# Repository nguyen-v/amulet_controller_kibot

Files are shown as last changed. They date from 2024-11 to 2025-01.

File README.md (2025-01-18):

<p align="center" width="100%">
  
</p>

<h1 align="center">Λmulet Motion Controller</h1>

<p align="center" width="100%">
  <a href="https://github.com/nguyen-v/amulet_controller_kibot/actions/workflows/ci.yaml">
    
  </a>
</p>

ΛMULET is a high-power brushless motor controller, compatible with the [moteus firmware](https://github.com/mjbots/moteus). It was specifically designed to be integrated in [EPFL Xplore](https://github.com/EPFLXplore)'s Legged Robot actuators.

<p align="center" width="100%">
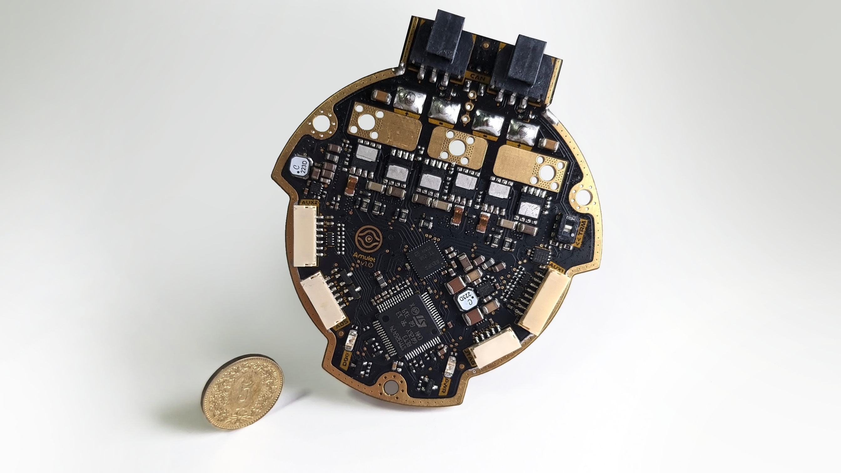
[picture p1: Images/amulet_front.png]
    
</p>

***

<p align="center">
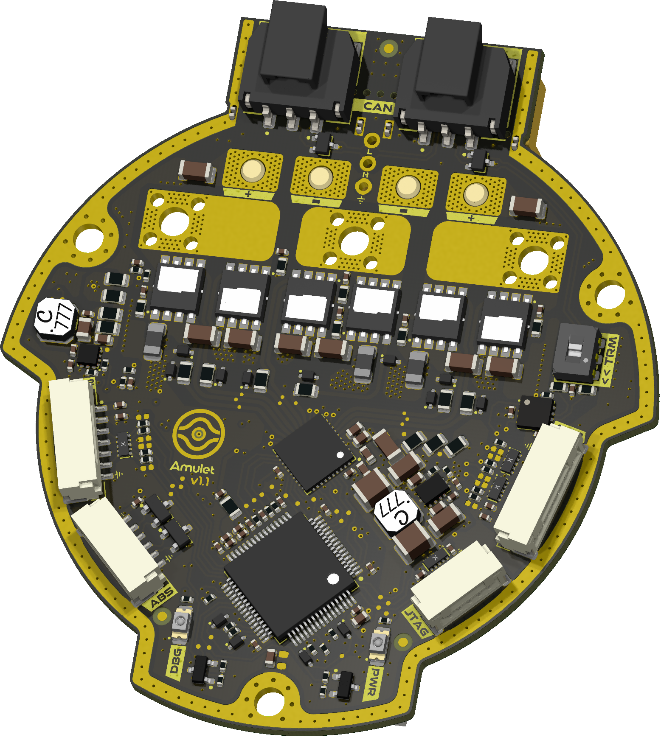
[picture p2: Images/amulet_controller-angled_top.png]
3D Top Angled
  
&nbsp; &nbsp; &nbsp; &nbsp;
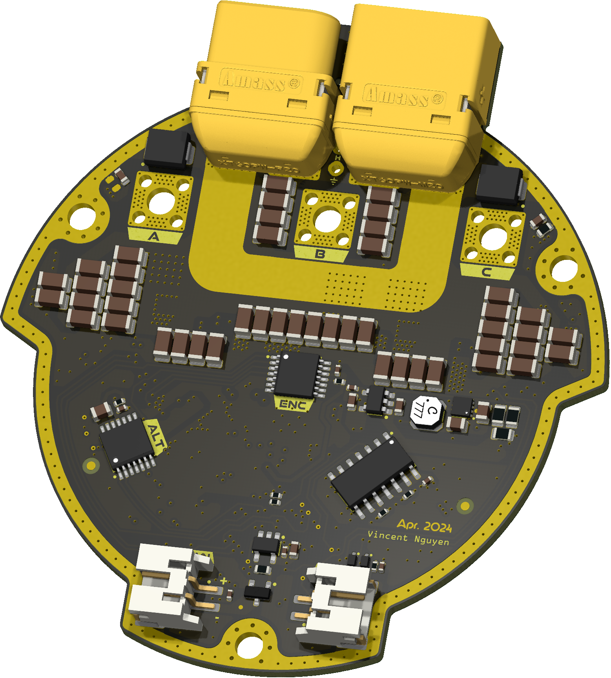
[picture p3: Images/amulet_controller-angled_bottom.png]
3D Bottom Angled
  
</p>

***

## SPECIFICATIONS

| Parameter | ΛMULET V1.0 | 
| --- | --- |
| Voltage Input | 12-44V |
| Peak Electrical Power | TBD |
| Mass | TBD |
| Peak Phase Current | 100A |
| Communication | 5Mbps CAN-FD |
| Cooling | 12V Fan |
| Positioning | 2x Onboard 14-bit Encoders |
| Control rate | 15-30kHz |
| PWM Switching Rate | 15-60kHz |
| MCU | STM32G474 |
| Dimensions | 69.67 × 76.7 mm |

***

## DIRECTORY STRUCTURE

    .
    ├─ Computations       # Misc calculations
    ├─ DXF_SVG            # Vector graphics
    ├─ HTML               # HTML files for generated webpage
    ├─ Images             # Pictures and renders
    │
    ├─ kibot_resources    # External resources for KiBot
    │  ├─ colors          # Color theme for KiCad
    │  ├─ fonts           # Fonts used in the project
    │  ├─ scripts         # External scripts used with KiBot
    │  └─ templates       # Templates for KiBot generated reports
    │
    ├─ kibot_yaml         # KiBot YAML config files
    ├─ KiRI               # KiRI (PCB diff viewer) files
    │
    ├─ lib                # KiCad footprint and symbol libraries
    │  ├─ 3d_models       # Component 3D models
    │  ├─ lib_fp          # Footprint libraries
    │  └─ lib_sym         # Symbol libraries
    │
    ├─ Logos              # Logos
    │
    ├─ Manufacturing      # Assembly and fabrication documents
    │  ├─ Assembly        # Assembly documents (BoM, pos, notes)
    │  │
    │  └─ Fabrication     # Fabrication documents (ZIP, notes)
    │     ├─ Drill Tables # CSV drill tables
    │     └─ Gerbers      # Gerbers
    │
    ├─ Report             # Reports for ERC/DRC
    ├─ Schematic          # PDF of schematic
    ├─ Templates          # Title block templates
    ├─ Testing
    │  └─ Testpoints      # Testpoints tables      
    │
    └─ Variants           # Outputs for assembly variants

***

## FIRMWARE

[Associated firmware](https://github.com/EPFLXplore/XRE_moteus/tree/amulet) is forked from the [moteus](https://github.com/mjbots/moteus) repository.

***

## CREDITS

Schematic is hugely inspired by the moteus controllers designed by Josh Pieper. They were modified to meet our own specifications, and to follow what I personally consider good layout practices.

***

## PHOTOS

<p align="center" width="100%">
    
</p>

<p align="center" width="100%">
    
</p>

<p align="center" width="100%">
    
</p>

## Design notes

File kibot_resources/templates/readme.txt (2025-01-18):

<p align="center" width="100%">
  
</p>

<h1 align="center">${BOARD_NAME}</h1>

<p align="center" width="100%">
  <a href="${GIT_URL}/actions/workflows/ci.yaml">
    CI Badge
  </a>
</p>

ΛMULET is a high-power brushless motor controller, compatible with the [moteus firmware](https://github.com/mjbots/moteus). It was specifically designed to be integrated in [EPFL Xplore](https://github.com/EPFLXplore)'s Legged Robot actuators.

<p align="center" width="100%">
    
</p>

***

<p align="center">
  3D Top Angled
&nbsp; &nbsp; &nbsp; &nbsp;
  3D Bottom Angled
</p>

***

## SPECIFICATIONS

| Parameter | ΛMULET V1.0 | 
| --- | --- |
| Voltage Input | 12-44V |
| Peak Electrical Power | TBD |
| Mass | TBD |
| Peak Phase Current | 100A |
| Communication | 5Mbps CAN-FD |
| Cooling | 12V Fan |
| Positioning | 2x Onboard 14-bit Encoders |
| Control rate | 15-30kHz |
| PWM Switching Rate | 15-60kHz |
| MCU | STM32G474 |
| Dimensions | ${bb_w_mm} × ${bb_h_mm} mm |

***

## DIRECTORY STRUCTURE

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

***

## FIRMWARE

[Associated firmware](https://github.com/EPFLXplore/XRE_moteus/tree/amulet) is forked from the [moteus](https://github.com/mjbots/moteus) repository.

***

## CREDITS

Schematic is hugely inspired by the moteus controllers designed by Josh Pieper. They were modified to meet our own specifications, and to follow what I personally consider good layout practices.

***

## PHOTOS

<p align="center" width="100%">
    
</p>

<p align="center" width="100%">
    
</p>

<p align="center" width="100%">
    
</p>

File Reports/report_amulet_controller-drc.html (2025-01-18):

Logo

| DRC report for amulet_controller
| PCB: amulet_controller Revision: 1.1.1+ (Unreleased) Date: 2025-01-18T22:40:42+0000 KiCad Version: 8.0.6 | Errors: 11 Warnings: 22 Total: 33

Violations

Type | Description | Details
clearance | Clearance violation (board minimum clearance 0.2000 mm; actual 0.0379 mm) | @(129.96 mm, 84.040001 mm): Pad 1 [/Project Architecture/Motor Control - Top Level/SC_P] of NT11 on L1 (Sig, PWR) @(129.76 mm, 83.09 mm): Pad 2 [/Project Architecture/Motor Control - Top Level/Motor Control - Inverter/SRC_LS_C] of R18 on L1 (Sig, PWR)
courtyards_overlap | Courtyards overlap | @(170.8504 mm, 87.9001 mm): Footprint U10 @(172.6404 mm, 96.4501 mm): Footprint J6
courtyards_overlap | Courtyards overlap | @(156.7504 mm, 54.1001 mm): Footprint J12 @(160.2004 mm, 61.2501 mm): Footprint D24
courtyards_overlap | Courtyards overlap | @(140.2504 mm, 54.1001 mm): Footprint J13 @(143.6504 mm, 61.2501 mm): Footprint D25
courtyards_overlap | Courtyards overlap | @(147.9 mm, 117.35 mm): Footprint C130 @(148.5004 mm, 122.0001 mm): Footprint H1
courtyards_overlap | Courtyards overlap | @(171.650401 mm, 90.100103 mm): Footprint C108 @(172.6404 mm, 96.4501 mm): Footprint J6
courtyards_overlap | Courtyards overlap | @(130.822731 mm, 107.70277 mm): Footprint J10 @(124.3404 mm, 96.4701 mm): Footprint J7
courtyards_overlap | Courtyards overlap | @(172.6404 mm, 96.4501 mm): Footprint J6 @(166.1754 mm, 107.6751 mm): Footprint J14
courtyards_overlap | Courtyards overlap | @(167.6 mm, 65.5 mm): Footprint D2 @(153.1504 mm, 64.7501 mm): Footprint J1
courtyards_overlap | Courtyards overlap | @(143.8504 mm, 64.7501 mm): Footprint J2 @(129.4 mm, 65.5 mm): Footprint D1
copper_edge_clearance | Board edge clearance violation (board setup constraints edge clearance 0.25 mm; actual 0.249999 mm) | @(132.3003 mm, 58.2043 mm): Arc on Edge.Cuts @(133.5004 mm, 58.7501 mm): PTH pad MP2 [CHASSIS] of J2
lib_footprint_mismatch | Footprint 'C_0402_1005_DensityHigh' does not match copy in library '0_capacitor_smd'. | @(165.802015 mm, 98.344758 mm): Footprint C124
lib_footprint_mismatch | Footprint '1054301203' does not match copy in library '0_connectors'. | @(156.7504 mm, 54.1001 mm): Footprint J12
lib_footprint_mismatch | Footprint 'R_0603_1608_DensityHigh' does not match copy in library '0_resistor_smd'. | @(149.1 mm, 117.35 mm): Footprint R52
lib_footprint_mismatch | Footprint 'C_0402_1005_DensityHigh' does not match copy in library '0_capacitor_smd'. | @(166.620577 mm, 95.251212 mm): Footprint C120
lib_footprint_mismatch | Footprint '1054301203' does not match copy in library '0_connectors'. | @(140.2504 mm, 54.1001 mm): Footprint J13
lib_footprint_mismatch | Footprint 'C_0402_1005_DensityHigh' does not match copy in library '0_capacitor_smd'. | @(167.243984 mm, 92.943938 mm): Footprint C118
lib_footprint_mismatch | Footprint 'C_0402_1005_DensityHigh' does not match copy in library '0_capacitor_smd'. | @(129.866333 mm, 92.694503 mm): Footprint C123
lib_footprint_mismatch | Footprint 'C_0402_1005_DensityHigh' does not match copy in library '0_capacitor_smd'. | @(167.451041 mm, 92.1712 mm): Footprint C116
lib_footprint_mismatch | Footprint 'C_0402_1005_DensityHigh' does not match copy in library '0_capacitor_smd'. | @(130.493965 mm, 95.036872 mm): Footprint C121
lib_footprint_mismatch | Footprint 'C_0402_1005_DensityHigh' does not match copy in library '0_capacitor_smd'. | @(130.701025 mm, 95.809613 mm): Footprint C119
lib_footprint_mismatch | Footprint 'C_0402_1005_DensityHigh' does not match copy in library '0_capacitor_smd'. | @(166.413521 mm, 96.023949 mm): Footprint C122
lib_footprint_mismatch | Footprint 'SOT1176D' does not match copy in library '0_package_DFN_QFN'. | @(128.472459 mm, 95.992643 mm): Footprint D17
lib_footprint_mismatch | Footprint 'C_0402_1005_DensityHigh' does not match copy in library '0_capacitor_smd'. | @(131.320291 mm, 98.127833 mm): Footprint C117
lib_footprint_mismatch | Footprint 'R_0603_1608_DensityHigh' does not match copy in library '0_resistor_smd'. | @(173.33 mm, 69.8 mm): Footprint R54
lib_footprint_mismatch | Footprint 'SOP-14_4.4x5mm_P0.65mm_H1.2mm' does not match copy in library '0_package_SO'. | @(166.253518 mm, 100.25 mm): Footprint U8
lib_footprint_mismatch | Footprint 'DIOM4336X24N' does not match copy in library '0_diode_smd'. | @(129.4 mm, 65.5 mm): Footprint D1
solder_mask_bridge | Front solder mask aperture bridges items with different nets | @(129.96 mm, 84.040001 mm): Pad 1 [/Project Architecture/Motor Control - Top Level/SC_P] of NT11 on L1 (Sig, PWR) @(129.76 mm, 83.09 mm): Pad 2 [/Project Architecture/Motor Control - Top Level/Motor Control - Inverter/SRC_LS_C] of R18 on L1 (Sig, PWR)
solder_mask_bridge | Front solder mask aperture bridges items with different nets | @(129.96 mm, 84.840001 mm): Pad 1 [/Project Architecture/Motor Control - Top Level/SC_N] of NT12 on L1 (Sig, PWR) @(129.76 mm, 85.79 mm): Pad 1 [GND] of R18 on L1 (Sig, PWR)
solder_mask_bridge | Front solder mask aperture bridges items with different nets | @(136.130445 mm, 93.156811 mm): Polygon on F.Mask @(136.0504 mm, 93.9001 mm): Via [/Project Architecture/Power - Generation/VOS_3V3] on L1 (Sig, PWR) - L6 (Sig, PWR)
solder_mask_bridge | Front solder mask aperture bridges items with different nets | @(157.7504 mm, 84.865 mm): Pad 1 [/Project Architecture/Motor Control - Top Level/SA_N] of NT6 on L1 (Sig, PWR) @(157.5754 mm, 85.79 mm): Pad 1 [GND] of R12 on L1 (Sig, PWR)
solder_mask_bridge | Front solder mask aperture bridges items with different nets | @(151.8996 mm, 84.0399 mm): Pad 1 [/Project Architecture/Motor Control - Top Level/SB_P] of NT8 on L1 (Sig, PWR) @(152.1 mm, 83.09 mm): Pad 2 [/Project Architecture/Motor Control - Top Level/Motor Control - Inverter/SRC_LS_B] of R15 on L1 (Sig, PWR)
solder_mask_bridge | Front solder mask aperture bridges items with different nets | @(151.8996 mm, 84.8399 mm): Pad 1 [/Project Architecture/Motor Control - Top Level/SB_N] of NT9 on L1 (Sig, PWR) @(152.1 mm, 85.79 mm): Pad 1 [GND] of R15 on L1 (Sig, PWR)

Generated by KiBot (https://github.com/INTI-CMNB/KiBot/) v1.8.3

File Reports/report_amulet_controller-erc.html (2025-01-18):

Logo

| ERC report for amulet_controller
| Schematic: amulet_controller Revision: 1.1.1+ (Unreleased) Date: 2025-01-18T22:40:34+0000 KiCad Version: 8.0.6 | Errors: 0 Warnings: 86 Total: 86

Sheet /Project Architecture/ (Project Architecture.kicad_sch)

Type | Description | Details
lib_symbol_issues | Symbol '+3V3' has been modified in library 'power' | @(1.9431 mm, 0.4953 mm): Symbol #PWR05 [+3V3]
lib_symbol_issues | Symbol '+5V' has been modified in library 'power' | @(1.905 mm, 0.4318 mm): Symbol #PWR04 [+5V]
lib_symbol_issues | Symbol '+12V' has been modified in library 'power' | @(1.8669 mm, 0.4953 mm): Symbol #PWR03 [+12V]

Sheet /Project Architecture/MCU - Power/ (MCU - Power.kicad_sch)

Type | Description | Details
lib_symbol_issues | Symbol 'GND' has been modified in library 'power' | @(1.4351 mm, 0.6223 mm): Symbol #PWR014 [GND]
lib_symbol_issues | Symbol '+3V3' has been modified in library 'power' | @(1.4351 mm, 0.4953 mm): Symbol #PWR013 [+3V3]
lib_symbol_issues | Symbol 'PWR_FLAG' has been modified in library 'power' | @(1.5367 mm, 0.9398 mm): Symbol #FLG01 [PWR_FLAG]
lib_symbol_issues | Symbol 'GND' has been modified in library 'power' | @(1.2827 mm, 1.0668 mm): Symbol #PWR011 [GND]
lib_symbol_issues | Symbol 'GND' has been modified in library 'power' | @(1.0414 mm, 1.1684 mm): Symbol #PWR010 [GND]
lib_symbol_issues | Symbol 'GND' has been modified in library 'power' | @(0.8128 mm, 0.8382 mm): Symbol #PWR08 [GND]
lib_symbol_issues | Symbol '+3V3' has been modified in library 'power' | @(0.8128 mm, 0.7112 mm): Symbol #PWR07 [+3V3]
lib_symbol_issues | Symbol 'GND' has been modified in library 'power' | @(1.8542 mm, 1.3081 mm): Symbol #PWR015 [GND]
lib_symbol_issues | Symbol 'GND' has been modified in library 'power' | @(1.2827 mm, 1.2573 mm): Symbol #PWR012 [GND]

Sheet /Project Architecture/MCU - IOs/ (MCU - IOs.kicad_sch)

Type | Description | Details
lib_symbol_issues | Symbol 'GND' has been modified in library 'power' | @(1.7018 mm, 1.778 mm): Symbol #PWR016 [GND]

Sheet /Project Architecture/Power - Generation/ (Power - Generation.kicad_sch)

Type | Description | Details
lib_symbol_issues | Symbol 'GND' has been modified in library 'power' | @(2.3114 mm, 2.0574 mm): Symbol #PWR020 [GND]
lib_symbol_issues | Symbol 'PWR_FLAG' has been modified in library 'power' | @(2.4257 mm, 1.143 mm): Symbol #FLG07 [PWR_FLAG]
lib_symbol_issues | Symbol 'GND' has been modified in library 'power' | @(2.3114 mm, 2.2225 mm): Symbol #PWR021 [GND]
lib_symbol_issues | Symbol 'GND' has been modified in library 'power' | @(2.3114 mm, 1.8923 mm): Symbol #PWR019 [GND]
lib_symbol_issues | Symbol 'PWR_FLAG' has been modified in library 'power' | @(1.5875 mm, 1.143 mm): Symbol #FLG04 [PWR_FLAG]
lib_symbol_issues | Symbol 'GND' has been modified in library 'power' | @(0.6477 mm, 1.524 mm): Symbol #PWR018 [GND]
lib_symbol_issues | Symbol 'PWR_FLAG' has been modified in library 'power' | @(3.175 mm, 0.5207 mm): Symbol #FLG08 [PWR_FLAG]
lib_symbol_issues | Symbol 'GND' has been modified in library 'power' | @(3.1115 mm, 1.5113 mm): Symbol #PWR023 [GND]
lib_symbol_issues | Symbol 'GND' has been modified in library 'power' | @(2.7305 mm, 0.889 mm): Symbol #PWR022 [GND]
lib_symbol_issues | Symbol 'PWR_FLAG' has been modified in library 'power' | @(0.4826 mm, 0.5207 mm): Symbol #FLG02 [PWR_FLAG]
lib_symbol_issues | Symbol 'GND' has been modified in library 'power' | @(0.6477 mm, 0.889 mm): Symbol #PWR017 [GND]
lib_symbol_issues | Symbol 'PWR_FLAG' has been modified in library 'power' | @(2.4257 mm, 0.5207 mm): Symbol #FLG06 [PWR_FLAG]
lib_symbol_issues | Symbol 'PWR_FLAG' has been modified in library 'power' | @(1.9939 mm, 0.8509 mm): Symbol #FLG05 [PWR_FLAG]
lib_symbol_issues | Symbol 'PWR_FLAG' has been modified in library 'power' | @(1.524 mm, 0.5207 mm): Symbol #FLG03 [PWR_FLAG]

Sheet /Project Architecture/Power - Connectors/ (Power - Connectors.kicad_sch)

Type | Description | Details
lib_symbol_issues | Symbol 'GND' has been modified in library 'power' | @(1.3589 mm, 0.9271 mm): Symbol #PWR024 [GND]

Sheet /Project Architecture/Motor Control - Top Level/ (Motor Control - Top Level.kicad_sch)

Type | Description | Details
lib_symbol_issues | Symbol 'GND' has been modified in library 'power' | @(1.4605 mm, 1.9685 mm): Symbol #PWR033 [GND]
lib_symbol_issues | Symbol 'GND' has been modified in library 'power' | @(1.7399 mm, 0.9652 mm): Symbol #PWR034 [GND]
lib_symbol_issues | Symbol 'GND' has been modified in library 'power' | @(1.2573 mm, 1.0922 mm): Symbol #PWR032 [GND]
lib_symbol_issues | Symbol '+3V3' has been modified in library 'power' | @(0.8255 mm, 1.7907 mm): Symbol #PWR026 [+3V3]
lib_symbol_issues | Symbol 'GND' has been modified in library 'power' | @(1.0541 mm, 0.762 mm): Symbol #PWR029 [GND]
lib_symbol_issues | Symbol '+3V3' has been modified in library 'power' | @(1.0287 mm, 1.016 mm): Symbol #PWR028 [+3V3]
lib_symbol_issues | Symbol 'GND' has been modified in library 'power' | @(1.1049 mm, 1.5875 mm): Symbol #PWR031 [GND]

Sheet /Project Architecture/Motor Control - Top Level/Motor Control - Inverter/ (Motor Control - Inverter.kicad_sch)

Type | Description | Details
lib_symbol_issues | Symbol 'GND' has been modified in library 'power' | @(0.3556 mm, 1.4224 mm): Symbol #PWR036 [GND]

Sheet /Project Architecture/Misc - Board Version, DAC/ (Misc - Board Version DAC.kicad_sch)

Type | Description | Details
lib_symbol_issues | Symbol 'GND' has been modified in library 'power' | @(1.4986 mm, 0.8128 mm): Symbol #PWR038 [GND]

Sheet /Project Architecture/User - LED Indicators/ (User - LED Indicators.kicad_sch)

Type | Description | Details
lib_symbol_issues | Symbol 'GND' has been modified in library 'power' | @(1.7653 mm, 1.1176 mm): Symbol #PWR040 [GND]
lib_symbol_issues | Symbol 'GND' has been modified in library 'power' | @(1.2827 mm, 1.1176 mm): Symbol #PWR039 [GND]
lib_symbol_issues | Symbol '+5V' has been modified in library 'power' | @(1.9812 mm, 0.5588 mm): Symbol #PWR041 [+5V]

Sheet /Project Architecture/Sensing - Temperature/ (Sensing - Temperature.kicad_sch)

Type | Description | Details
lib_symbol_issues | Symbol 'GND' has been modified in library 'power' | @(1.7653 mm, 1.1176 mm): Symbol #PWR044 [GND]
lib_symbol_issues | Symbol 'GND' has been modified in library 'power' | @(0.9779 mm, 1.1176 mm): Symbol #PWR042 [GND]

Sheet /Project Architecture/Sensing - Battery/ (Sensing - Battery.kicad_sch)

Type | Description | Details
lib_symbol_issues | Symbol 'GND' has been modified in library 'power' | @(1.3462 mm, 0.9271 mm): Symbol #PWR046 [GND]

Sheet /Project Architecture/Sensing - Position/ (Sensing - Position.kicad_sch)

Type | Description | Details
lib_symbol_issues | Symbol '+3V3' has been modified in library 'power' | @(0.508 mm, 0.6604 mm): Symbol #PWR047 [+3V3]
lib_symbol_issues | Symbol 'PWR_FLAG' has been modified in library 'power' | @(0.8001 mm, 0.6858 mm): Symbol #FLG09 [PWR_FLAG]
lib_symbol_issues | Symbol 'GND' has been modified in library 'power' | @(0.508 mm, 1.1049 mm): Symbol #PWR048 [GND]
lib_symbol_issues | Symbol 'GND' has been modified in library 'power' | @(2.2098 mm, 0.8001 mm): Symbol #PWR051 [GND]
lib_symbol_issues | Symbol 'PWR_FLAG' has been modified in library 'power' | @(2.2098 mm, 0.6858 mm): Symbol #FLG010 [PWR_FLAG]
lib_symbol_issues | Symbol '+3V3' has been modified in library 'power' | @(1.7526 mm, 0.6604 mm): Symbol #PWR049 [+3V3]
lib_symbol_issues | Symbol 'GND' has been modified in library 'power' | @(1.7526 mm, 1.1176 mm): Symbol #PWR050 [GND]

Sheet /Project Architecture/Interface - RS-422/ (Interface - RS-422.kicad_sch)

Type | Description | Details
lib_symbol_issues | Symbol '+3V3' has been modified in library 'power' | @(1.4732 mm, 0.5334 mm): Symbol #PWR054 [+3V3]
lib_symbol_issues | Symbol 'GND' has been modified in library 'power' | @(1.4605 mm, 1.0922 mm): Symbol #PWR053 [GND]
lib_symbol_issues | Symbol 'GND' has been modified in library 'power' | @(1.2827 mm, 0.6477 mm): Symbol #PWR052 [GND]

Sheet /Project Architecture/Interface - FD-CAN/ (Interface - FD-CAN.kicad_sch)

Type | Description | Details
lib_symbol_issues | Symbol '+5V' has been modified in library 'power' | @(1.7018 mm, 0.6477 mm): Symbol #PWR058 [+5V]
lib_symbol_issues | Symbol '+3V3' has been modified in library 'power' | @(1.3462 mm, 0.6477 mm): Symbol #PWR056 [+3V3]
lib_symbol_issues | Symbol 'GND' has been modified in library 'power' | @(1.7018 mm, 0.7747 mm): Symbol #PWR059 [GND]
lib_symbol_issues | Symbol 'GND' has been modified in library 'power' | @(1.2954 mm, 1.1303 mm): Symbol #PWR055 [GND]
lib_symbol_issues | Symbol 'GND' has been modified in library 'power' | @(1.3462 mm, 0.7747 mm): Symbol #PWR057 [GND]

Sheet /Project Architecture/Interface - Fan Control/ (Interface - Fan Control.kicad_sch)

Type | Description | Details
lib_symbol_issues | Symbol 'GND' has been modified in library 'power' | @(1.3589 mm, 1.0795 mm): Symbol #PWR062 [GND]
lib_symbol_issues | Symbol 'GND' has been modified in library 'power' | @(1.0414 mm, 0.7874 mm): Symbol #PWR060 [GND]
lib_symbol_issues | Symbol '+5V' has been modified in library 'power' | @(1.3589 mm, 0.6477 mm): Symbol #PWR061 [+5V]

Sheet /Project Architecture/Interface - Interconnects/ (Interface - Interconnects.kicad_sch)

Type | Description | Details
lib_symbol_issues | Symbol '+12V' has been modified in library 'power' | @(1.7653 mm, 2.5146 mm): Symbol #PWR077 [+12V]
lib_symbol_issues | Symbol 'GND' has been modified in library 'power' | @(2.6797 mm, 2.2733 mm): Symbol #PWR081 [GND]
lib_symbol_issues | Symbol 'GND' has been modified in library 'power' | @(2.6924 mm, 0.7493 mm): Symbol #PWR082 [GND]
lib_symbol_issues | Symbol 'GND' has been modified in library 'power' | @(2.7051 mm, 0.9906 mm): Symbol #PWR083 [GND]
lib_symbol_issues | Symbol 'GND' has been modified in library 'power' | @(3.5941 mm, 0.8636 mm): Symbol #PWR089 [GND]
lib_symbol_issues | Symbol '+3V3' has been modified in library 'power' | @(2.8194 mm, 1.3716 mm): Symbol #PWR086 [+3V3]
lib_symbol_issues | Symbol 'GND' has been modified in library 'power' | @(2.8575 mm, 1.4224 mm): Symbol #PWR088 [GND]
lib_symbol_issues | Symbol '+5V' has been modified in library 'power' | @(2.6797 mm, 1.8923 mm): Symbol #PWR080 [+5V]
lib_symbol_issues | Symbol 'GND' has been modified in library 'power' | @(2.7178 mm, 1.9558 mm): Symbol #PWR085 [GND]
lib_symbol_issues | Symbol 'GND' has been modified in library 'power' | @(2.8194 mm, 1.6764 mm): Symbol #PWR087 [GND]
lib_symbol_issues | Symbol 'GND' has been modified in library 'power' | @(1.8288 mm, 2.6035 mm): Symbol #PWR078 [GND]
lib_symbol_issues | Symbol 'GND' has been modified in library 'power' | @(0.6604 mm, 1.0922 mm): Symbol #PWR070 [GND]
lib_symbol_issues | Symbol 'GND' has been modified in library 'power' | @(0.6604 mm, 2.0447 mm): Symbol #PWR071 [GND]
lib_symbol_issues | Symbol '+5V' has been modified in library 'power' | @(0.5715 mm, 0.5334 mm): Symbol #PWR066 [+5V]
lib_symbol_issues | Symbol 'GND' has been modified in library 'power' | @(0.8255 mm, 0.6223 mm): Symbol #PWR074 [GND]
lib_symbol_issues | Symbol '+3V3' has been modified in library 'power' | @(0.7747 mm, 0.5334 mm): Symbol #PWR072 [+3V3]
lib_symbol_issues | Symbol 'GND' has been modified in library 'power' | @(0.6223 mm, 0.6223 mm): Symbol #PWR068 [GND]
lib_symbol_issues | Symbol '+5V' has been modified in library 'power' | @(0.5715 mm, 1.5113 mm): Symbol #PWR067 [+5V]
lib_symbol_issues | Symbol '+3V3' has been modified in library 'power' | @(0.7747 mm, 1.5113 mm): Symbol #PWR073 [+3V3]
lib_symbol_issues | Symbol 'GND' has been modified in library 'power' | @(0.6223 mm, 1.6002 mm): Symbol #PWR069 [GND]
lib_symbol_issues | Symbol 'GND' has been modified in library 'power' | @(0.8255 mm, 1.6002 mm): Symbol #PWR075 [GND]

Sheet /Project Architecture/Misc - Holes, Fiducials/ (Misc - Holes Fiducials.kicad_sch)

Type | Description | Details
lib_symbol_issues | Symbol 'PWR_FLAG' has been modified in library 'power' | @(1.1049 mm, 0.8636 mm): Symbol #FLG011 [PWR_FLAG]
lib_symbol_issues | Symbol 'GND' has been modified in library 'power' | @(1.7907 mm, 1.016 mm): Symbol #PWR095 [GND]
lib_symbol_issues | Symbol 'GND' has been modified in library 'power' | @(1.3843 mm, 1.016 mm): Symbol #PWR093 [GND]
lib_symbol_issues | Symbol 'GND' has been modified in library 'power' | @(0.9906 mm, 1.016 mm): Symbol #PWR091 [GND]

Generated by KiBot (https://github.com/INTI-CMNB/KiBot/) v1.8.3

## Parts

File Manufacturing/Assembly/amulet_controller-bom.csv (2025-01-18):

Row | Quantity Per PCB | References | Value | Datasheet | Footprint | Description | Manufacturer | Manufacturer Part Number | Supplier 1 | Supplier Part Number 1
1 | 3 | C12 C13 C14 | 1n X7R 25V | https://www.yageo.com/upload/media/product/app/datasheet/mlcc/upy-ac_np0x7rx7s_6_3v-to-2kv.pdf | C_0402_1005_DensityHigh | 1000 pF ±10% 25V Ceramic Capacitor X7R 0402 (1005 Metric) | YAGEO | AC0402KRX7R8BB102 | Digikey | 311-3065-1-ND
2 | 6 | C133 C134 C135 C136 C137 C138 | 3n3 X7R 100V | https://search.murata.co.jp/Ceramy/image/img/A01X/G101/ENG/GRM155R72A332KA01-01.pdf | C_0402_1005_DensityHigh | 3300 pF ±10% 100V Ceramic Capacitor X7R 0402 (1005 Metric) | Murata Electronics | GRM155R72A332KA01D | Digikey | 490-8261-1-ND
3 | 1 | C129 | 4n7 X7R 100V | https://www.murata.com/-/media/webrenewal/support/library/catalog/products/k35e.ashx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 | C_0402_1005_DensityHigh | 4700 pF ±10% 100V Ceramic Capacitor X7R 0402 (1005 Metric) | Murata Electronics | GCM155R72A472KA37D | Digikey | 490-4765-1-ND
4 | 1 | C76 | 10n X7R 100V | https://mm.digikey.com/Volume0/opasdata/d220001/medias/docus/2615/HMR105B7103KV-F_SS.pdf | C_0402_1005_DensityHigh | 10000 pF ±10% 100V Ceramic Capacitor X7R 0402 (1005 Metric) | Taiyo Yuden | HMR105B7103KV-F | Digikey | 587-HMR105B7103KV-FCT-ND
5 | 1 | C91 | 47n X7R 100V | https://connect.kemet.com:7667/gateway/IntelliData-ComponentDocumentation/1.0/download/datasheet/C0603C473K1RECAUTO | C_0603_1608_DensityHigh | 0.047 µF ±10% 100V Ceramic Capacitor X7R 0603 (1608 Metric) | KEMET | C0603C473K1RECAUTO | Digikey | 399-14764-1-ND
6 | 26 | C3 C4 C5 C8 C10 C11 C27 C28 C29 C101 C102 C103 C104 C105 C107 C108 C109 C111 C112 C113 C114 C115 C125 C126 C127 C128 | 100n X7R 50V | https://search.murata.co.jp/Ceramy/image/img/A01X/G101/ENG/GCM155R71H104KE02-01.pdf | C_0402_1005_DensityHigh | 0.1 µF ±10% 50V Ceramic Capacitor X7R 0402 (1005 Metric) | Murata Electronics | GCM155R71H104KE02J | Digikey | 490-14514-1-ND
7 | 2 | C22 C92 | 100n X7R 100V | https://mm.digikey.com/Volume0/opasdata/d220001/medias/docus/21/HMK107B7104KAHT_SS.pdf | C_0603_1608_DensityHigh | 0.1 µF ±10% 100V Ceramic Capacitor X7R 0603 (1608 Metric) | Taiyo Yuden | HMK107B7104KAHT | Digikey | 587-6009-1-ND
8 | 1 | C90 | 100n X7R 16V | https://search.murata.co.jp/Ceramy/image/img/A01X/G101/ENG/GCM155R71C104KA55-01.pdf | C_0402_1005_DensityHigh | 0.1 µF ±10% 16V Ceramic Capacitor X7R 0402 (1005 Metric) | Murata Electronics | GCM155R71C104KA55D | Digikey | 490-4759-1-ND
9 | 3 | C95 C97 C99 | 100n X7R 100V | https://connect.kemet.com:7667/gateway/IntelliData-ComponentDocumentation/1.0/download/datasheet/C1206C104K1RACAUTO | C_1206_3216_DensityHighest | 0.1 µF ±10% 100V Ceramic Capacitor X7R 1206 (3216 Metric) | KEMET | C1206C104K1RACAUTO | Digikey | 399-7008-1-ND
10 | 2 | C23 C25 | 220n X7S 100V | https://mm.digikey.com/Volume0/opasdata/d220001/medias/docus/2249/TMK105B7224KV-FR_SS.pdf | C_0603_1608_DensityHigh | 0.22 µF ±10% 100V Ceramic Capacitor X7S 0603 (1608 Metric) | Taiyo Yuden | HMK107C7224KAHTE | Digikey | 587-5012-1-ND
11 | 5 | C2 C6 C9 C24 C26 | 1u X7R 10V | https://search.murata.co.jp/Ceramy/image/img/A01X/G101/ENG/GRM155Z71A105KE01-01A.pdf | C_0402_1005_DensityHigh | 1 µF ±10% 10V Ceramic Capacitor X7R 0402 (1005 Metric) | Murata Electronics | GRM155Z71A105KE01J | Digikey | 490-GRM155Z71A105KE01JCT-ND
12 | 3 | C60 C88 C93 | 1u X7R 25V | https://mm.digikey.com/Volume0/opasdata/d220001/medias/docus/2146/TMK107AB7105KAHT_SS.pdf | C_0603_1608_DensityHigh | 1 µF ±10% 25V Ceramic Capacitor X7R 0603 (1608 Metric) | Taiyo Yuden | TMK107AB7105KAHT | Digikey | 587-3467-1-ND
13 | 1 | C94 | 1u X7R 6.3V | https://search.murata.co.jp/Ceramy/image/img/A01X/G101/ENG/GRT155R70J105KE01-01.pdf | C_0402_1005_DensityHigh | 1 µF ±10% 6.3V Ceramic Capacitor X7R 0402 (1005 Metric) | Murata Electronics | GRT155R70J105KE01D | Digikey | 490-18216-1-ND
14 | 7 | C15 C16 C17 C18 C20 C45 C52 | 2u2 X7R 100V | https://product.tdk.com/system/files/dam/doc/product/capacitor/ceramic/mlcc/catalog/mlcc_automotive_midvoltage_en.pdf | R_0805_2012_DensityHigh | Multilayer Ceramic Capacitors MLCC - SMD/SMT 0805 100VDC 2.2uF 10% 1.25mm AEC-Q200 | TDK Corporation | CGA4J1X7R2A225K125AC | Mouser | 810-CGA4J7R2A225K125
15 | 3 | C1 C84 C110 | 4u7 X7R 16V | https://search.murata.co.jp/Ceramy/image/img/A01X/G101/ENG/GRM188Z71C475KE21-01A.pdf | C_0603_1608_DensityHigh | 4.7 µF ±10% 16V Ceramic Capacitor X7R 0603 (1608 Metric) | Murata Electronics | GRM188Z71C475KE21J | Digikey | 490-GRM188Z71C475KE21JCT-ND
16 | 54 | C19 C21 C31 C32 C33 C34 C35 C36 C39 C40 C41 C42 C43 C44 C46 C47 C48 C49 C50 C51 C53 C54 C55 C57 C58 C59 C61 C62 C63 C64 C65 C66 C67 C68 C69 C70 C71 C72 C73 C74 C75 C77 C78 C79 C80 C81 C82 C85 C86 C87 C89 C96 C98 C100 | 4u7 X7R 100V | https://search.murata.co.jp/Ceramy/image/img/A01X/G101/ENG/GRJ31CZ72A475KE01-01.pdf | C_1206_3216_DensityHigh | 4.7 µF ±10% 100V Ceramic Capacitor X7R 1206 (3216 Metric) | Murata Electronics | GRJ31CZ72A475KE01L | Digikey | 490-GRJ31CZ72A475KE01LCT-ND
17 | 1 | C7 | 4u7 X5R 25V | https://www.mouser.ch/datasheet/2/40/CM_Series_e-2835982.pdf | C_0402_1005_DensityHigh | 4.7 µF ±20% 25V Ceramic Capacitor X5R 0402 (1005 Metric) | KYOCERA AVX | CM05X5R475M25AH | Mouser | 581-CM05X5R475M25AH
18 | 2 | C56 C106 | 10u X7R 25V | https://search.murata.co.jp/Ceramy/image/img/A01X/G101/ENG/GRM21BZ71E106KE15-01.pdf | C_0805_2012_DensityHighest | 10 µF ±10% 25V Ceramic Capacitor X7R 0805 (2012 Metric) | Murata Electronics | GRM21BZ71E106KE15L | Digikey | 490-GRM21BZ71E106KE15LCT-ND
19 | 2 | C30 C38 | 15u X7R 25V | https://product.tdk.com/system/files/dam/doc/product/capacitor/ceramic/mlcc/catalog/mlcc_automotive_general_en.pdf | C_1210_3225_DensityHigh | 15 µF ±20% 25V Ceramic Capacitor X7R 1210 (3225 Metric) | TDK Corporation | CGA6M3X7R1E156M200AB | Digikey | 445-175431-1-ND
20 | 2 | C37 C83 | 22u X7R 10V | https://search.murata.co.jp/Ceramy/image/img/A01X/G101/ENG/GRM21BZ71A226ME15-01.pdf | C_0805_2012_DensityHighest | 22 µF ±20% 10V Ceramic Capacitor X7R 0805 (2012 Metric) | Murata Electronics | GRM21BZ71A226ME15L | Digikey | 490-GRM21BZ71A226ME15LCT-ND
21 | 3 | C130 C131 C132 | 1n X7R 1kV | https://connect.kemet.com:7667/gateway/IntelliData-ComponentDocumentation/1.0/download/specsheet/C0603V102KDRAC7867 | C_0603_1608_DensityHigh | 1000 pF ±10% 1000V (1kV) Ceramic Capacitor X7R 0603 (1608 Metric) | KEMET | C0603V102KDRAC7867 | Digikey | 399-12306-1-ND
22 | 15 | D3 D4 D5 D6 D7 D8 D9 D10 D11 D14 D15 D19 D20 D21 D22 | BAT41KFILM | https://www.st.com/content/ccc/resource/technical/document/datasheet/5b/cd/d8/0a/45/56/41/6c/CD00130227.pdf/files/CD00130227.pdf/jcr:content/translations/en.C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 | D_SOD-523 | Diode 100 V 200mA Surface Mount SOD-523 | STMicroelectronics | BAT41KFILM | Digikey | 497-5556-1-ND
23 | 2 | D23 D27 | CDSOT23-SM712 | https://www.bourns.com/docs/Product-Datasheets/CDSOT23-SM712.pdf | SOT95P230X110-3N | 26V, 14V Clamp 17A (8/20µs) Ipp Tvs Diode Surface Mount SOT-23-3 | Bourns Inc. | CDSOT23-SM712 | Digikey | CDSOT23-SM712CT-ND
24 | 1 | D13 | GREEN | https://www.bivar.com/parts_content/Datasheets/SM1206NPGC-IL.pdf | LED_SM1206 | Green 525nm LED Indication - Discrete 3V 1206 (3216 Metric) | Bivar Inc. | SM1206NPGC-IL | Digikey | 492-1945-1-ND
25 | 2 | D24 D25 | PESD2CANFD24V-UX | https://assets.nexperia.com/documents/data-sheet/PESD2CANFD24V-U.pdf | SOT95P230X117-3N | 42V Clamp 2.6A (8/20µs) Ipp Tvs Diode Surface Mount SOT-323 | Nexperia USA Inc. | PESD2CANFD24V-UX | Digikey | 1727-PESD2CANFD24V-UXCT-ND
26 | 2 | D18 D26 | PESD4USB3U-TBSX | https://assets.nexperia.com/documents/data-sheet/PESD4USB3U-TBS.pdf | SOT1176D | 3.5V (Typ) Clamp 7A (8/20µs) Ipp Tvs Diode Surface Mount, Wettable Flank DFN2510D-10 | Nexperia USA Inc. | PESD4USB3U-TBSX | Digikey | 1727-PESD4USB3U-TBSXCT-ND
27 | 2 | D16 D17 | PESD4USB5B-TBSX | https://assets.nexperia.com/documents/data-sheet/PESD4USB5B-TBS.pdf | SOT1176D | 5.5V (Typ) Clamp 7A (8/20µs) Ipp Tvs Diode Surface Mount, Wettable Flank DFN2510D-10 | Nexperia USA Inc. | PESD4USB5B-TBSX | Digikey | 1727-PESD4USB5B-TBSXCT-ND
28 | 2 | D1 D2 | SMBJ51CD-M3/H | https://www.vishay.com/docs/87606/smbj5cdthrusmbj120cd.pdf | DIOM4336X24N | Surface-Mount TRANSZORB® Transient Voltage Suppressors | Vishay | SMBJ51CD-M3/H | Digikey | SMBJ51CD-M3/HGICT-ND
29 | 1 | D12 | YELLOW | https://www.bivar.com/parts_content/Datasheets/SM1206NYC-IL.pdf | LED_SM1206 | Yellow 592nm LED Indication - Discrete 2V 1206 (3216 Metric) | Bivar Inc. | SM1206NYC-IL | Digikey | 492-1947-1-ND
30 | 4 | FB1 FB2 FB3 FB4 | 1k @ 100MHz | https://www.we-online.com/katalog/datasheet/742792096.pdf | R_0805_2012_DensityHigh | 1 kOhms @ 100 MHz 1 Signal Line Ferrite Bead 0805 (2012 Metric) 1A 300mOhm | Würth Elektronik | 742792096 | Digikey | 732-4648-1-ND
31 | 2 | J12 J13 | Nano-Fit 1x03 | https://www.literature.molex.com/SQLImages/kelmscott/Molex/PDF_Images/987651-1223.PDF | 1054301203 | Connector Header Surface Mount, Right Angle 3 position 0.098" (2.50mm) | Molex | 1054301203 | Digikey | WM26098CT-ND
32 | 2 | J8 J9 | S2B-PH-SM4-TB | https://www.jst-mfg.com/product/pdf/eng/ePH.pdf | JST_PH_S2B-PH-SM4-TB_1x02-1MP_P2.00mm_Horizontal | Connector Header Surface Mount, Right Angle 2 position 0.079" (2.00mm) | JST Sales America Inc. | S2B-PH-SM4-TB | Digikey | 455-S2B-PH-SM4-TBCT-ND
33 | 1 | J14 | SM05B-GHS-TB | https://www.jst-mfg.com/product/pdf/eng/eGH.pdf | JST_GH_SM05B-GHS-TB_1x05-1MP_P1.25mm_Horizontal | Connector Header Surface Mount, Right Angle 5 position 0.049" (1.25mm) | JST Sales America Inc. | SM05B-GHS-TB | Digikey | 455-SM05B-GHS-TBCT-ND
34 | 1 | J10 | SM06B-GHS-TB | https://www.jst-mfg.com/product/pdf/eng/eGH.pdf | JST_GH_SM06B-GHS-TB_1x06-1MP_P1.25mm_Horizontal | Connector Header Surface Mount, Right Angle 6 position 0.049" (1.25mm) | JST Sales America Inc. | SM06B-GHS-TB | Digikey | 455-1568-1-ND
35 | 1 | J7 | SM07B-GHS-TB | https://www.jst-mfg.com/product/pdf/eng/eGH.pdf | JST_GH_SM07B-GHS-TB_1x07-1MP_P1.25mm_Horizontal | Connector Header Surface Mount, Right Angle 7 position 0.049" (1.25mm) | JST Sales America Inc. | SM07B-GHS-TB(LF)(SN) | Digikey | 455-1569-1-ND
36 | 1 | J6 | SM08B-GHS-TB | https://www.jst-mfg.com/product/pdf/eng/eGH.pdf | JST_GH_SM08B-GHS-TB_1x08-1MP_P1.25mm_Horizontal | Connector Header Surface Mount, Right Angle 8 position 0.049" (1.25mm) | JST Sales America Inc. | SM08B-GHS-TB | Digikey | 455-1570-1-ND
37 | 1 | J1 | XT60PW-F | https://www.tme.eu/Document/1191bc2fa3aee3c446e5a895fd8f7983/XT60PW-F.pdf | AMASS_XT60PW-F_1x02_P7.20mm_Horizontal | Socket; DC supply; XT60; female; PIN: 2; on PCBs; THT; yellow; 30A | AMASS | XT60PW-F | Transfer Multisort Elektronik | XT60PW-F
38 | 1 | J2 | XT60PW-M | https://www.tme.eu/Document/b13629717d44ae038681dba08d18c0b6/XT60PW-M.pdf | AMASS_XT60PW-M_1x02_P7.20mm_Horizontal | Socket; DC supply; XT60; male; PIN: 2; on PCBs; THT; yellow; 30A; 500V | AMASS | XT60PW-M | Transfer Multisort Elektronik | XT60PW-M
39 | 1 | L3 | 2u2 | https://www.coilcraft.com/getmedia/3ba581dc-6d87-4be6-9dea-9167ac97554d/lps3314.pdf | L_Coilcraft_LPS3314 | Power Inductors - SMD 2.2uH Shld 20% 1.2A 100 mOhms | Coilcraft | LPS3314-222MRC | Mouser | 994-LPS3314-222MRC
40 | 2 | L1 L2 | 22u | https://www.coilcraft.com/getmedia/31b05c96-4c4c-4498-8dbb-fe092de76bad/lps4018.pdf | L_Coilcraft_LPS4018 | Power Inductors - SMD 22uH Shld 20% 830mA 360 mOhms | Coilcraft | LPS4018-223MRC | Mouser | 994-LPS4018-223MRC
41 | 3 | Q7 Q8 Q9 | PMV90ENER | https://assets.nexperia.com/documents/data-sheet/PMV90ENE.pdf | SOT-23-3 | N-Channel 30 V 3A (Ta) 460mW (Ta) Surface Mount TO-236AB | Nexperia USA Inc. | PMV90ENER | Digikey | 1727-2735-1-ND
42 | 6 | Q1 Q2 Q3 Q4 Q5 Q6 | TPW1R306PL,L1Q | https://toshiba.semicon-storage.com/info/TPW1R306PL_datasheet_en_20191021.pdf?did=55843&prodName=TPW1R306PL | 2-5S1A | N-Channel 60 V 260A (Tc) 960mW (Ta), 170W (Tc) Surface Mount 8-DSOP Advance | Toshiba Semiconductor and Storage | TPW1R306PL,L1Q | Digikey | TPW1R306PLL1QCT-ND
43 | 3 | R12 R15 R18 | 0m5 1% 2W | https://www.seielect.com/catalog/sei-hcs.pdf | HCS1206FTL500 | 0.5 mOhms ±1% 2W Chip Resistor 1206 (3216 Metric) Automotive AEC-Q200, Current Sense, Moisture Resistant Metal Element | Stackpole Electronics Inc | HCS1206FTL500 | Digikey | HCS1206FTL500CT-ND
44 | 3 | R4 R31 R32 | 0R | https://industrial.panasonic.com/ww/products/pt/general-purpose-chip-resistors/models/ERJ2GE0R00X | R_0402_1005_DensityHigh | 0 Ohms Jumper Chip Resistor 0402 (1005 Metric) Automotive AEC-Q200 Thick Film | Panasonic Electronic Components | ERJ-2GE0R00X | Digikey | P0.0JCT-ND
45 | 1 | R53 | 0R | https://www.vishay.com/docs/20043/crcwhpe3.pdf | R_0603_1608_DensityHigh | 0 Ohms Jumper Chip Resistor 0603 (1608 Metric) Automotive AEC-Q200, Pulse Withstanding Thick Film | Vishay | CRCW06030000Z0EAHP | Digikey | 541-0.0SBCT-ND
46 | 6 | R55 R56 R57 R58 R59 R60 | 5R 1% 0.4W | https://www.seielect.com/catalog/sei-csrt.pdf | R_0603_1608_DensityHigh | 5 Ohms ±1% 0.4W Chip Resistor 0603 (1608 Metric) Automotive AEC-Q200, Current Sense Thin Film | Stackpole Electronics Inc | CSRT0603FT5R00 | Digikey | 738-CSRT0603FT5R00CT-ND
47 | 6 | R10 R11 R13 R14 R16 R17 | 7R5 1% 1/2W | https://www.vishay.com/docs/20043/crcwhpe3.pdf | R_0805_2012_DensityHigh | 7.5 Ohms ±1% 0.5W, 1/2W Chip Resistor 0805 (2012 Metric) Automotive AEC-Q200, Pulse Withstanding Thick Film | Vishay | CRCW08057R50FKEAHP | Digikey | 541-7.50TCT-ND
48 | 1 | R34 | 10R 1% | https://www.vishay.com/docs/20043/crcwhpe3.pdf | R_0603_1608_DensityHigh | 10 Ohms ±1% 0.333W, 1/3W Chip Resistor 0603 (1608 Metric) Automotive AEC-Q200, Pulse Withstanding Thick Film | Vishay | CRCW060310R0FKEAHP | Digikey | 541-10.0SCT-ND
49 | 3 | R1 R2 R3 | 22R 1% | https://industrial.panasonic.com/cdbs/www-data/pdf/RDA0000/AOA0000C304.pdf | R_0402_1005_DensityHigh | 22 Ohms ±1% 0.1W, 1/10W Chip Resistor 0402 (1005 Metric) Automotive AEC-Q200 Thick Film | Panasonic Electronic Components | ERJ-2RKF22R0X | Digikey | P22.0LCT-ND
50 | 2 | R50 R51 | 60R4 1% 1/4W | https://www.rohm.com/datasheet?p=ESR01MZPF&dist=Digi-key&media=referral&campaign=Digi-key | R_0603_1608_DensityHigh | 60.4 Ohms ±1% 0.25W, 1/4W Chip Resistor 0603 (1608 Metric) Automotive AEC-Q200, Pulse Withstanding Thick Film | Rohm Semiconductor | ESR03EZPF60R4 | Digikey | 511-ESR03EZPF60R4CT-ND
51 | 14 | R22 R23 R25 R35 R36 R37 R38 R39 R40 R41 R42 R43 R48 R49 | 100R 1% 1/5W | https://www.vishay.com/docs/20065/rcse3.pdf | R_0402_1005_DensityHigh | 100 Ohms ±1% 0.2W, 1/5W Chip Resistor 0402 (1005 Metric) Automotive AEC-Q200, Pulse Withstanding Thick Film | Vishay | RCS0402100RFKED | Digikey | 541-2886-1-ND
52 | 1 | R26 | 150R 1% 1/5W | https://www.vishay.com/docs/20065/rcse3.pdf | R_0402_1005_DensityHigh | 150 Ohms ±1% 0.2W, 1/5W Chip Resistor 0402 (1005 Metric) Automotive AEC-Q200, Pulse Withstanding Thick Film | Vishay | RCS0402150RFKED | Digikey | 541-4373-1-ND
53 | 7 | R8 R9 R28 R44 R45 R46 R47 | 2k 1% | https://industrial.panasonic.com/cdbs/www-data/pdf/RDA0000/AOA0000C304.pdf | R_0402_1005_DensityHigh | 2 kOhms ±1% 0.1W, 1/10W Chip Resistor 0402 (1005 Metric) Automotive AEC-Q200 Thick Film | Vishay | ERJ-2RKF2001X | Digikey | P2.00KLCT-ND
54 | 1 | R30 | 4k7 1% | https://www.yageo.com/upload/media/product/app/datasheet/rchip/pyu-rt_1-to-0.01_rohs_l.pdf | R_0402_1005_DensityHigh | 4.7 kOhms ±1% 0.063W, 1/16W Chip Resistor 0402 (1005 Metric) Moisture Resistant Thin Film | YAGEO | RT0402FRE134K7L | Digikey | 13-RT0402FRE134K7LCT-ND
55 | 1 | R6 | 9k09 1% | https://www.yageo.com/upload/media/product/app/datasheet/rchip/pyu-rt_1-to-0.01_rohs_l.pdf | R_0402_1005_DensityHigh | 9.09 kOhms ±1% 0.063W, 1/16W Chip Resistor 0402 (1005 Metric) Thin Film | YAGEO | RT0402FRE079K09L | Digikey | 13-RT0402FRE079K09LCT-ND
56 | 3 | R7 R27 R33 | 10k 1% | https://www.yageo.com/upload/media/product/app/datasheet/rchip/pyu-rt_1-to-0.01_rohs_l.pdf | R_0402_1005_DensityHigh | 10 kOhms ±1% 0.063W, 1/16W Chip Resistor 0402 (1005 Metric) Thin Film | YAGEO | RT0402FRE0710KL | Digikey | YAG1233CT-ND
57 | 6 | R5 R19 R20 R21 R24 R29 | 100k 1% | https://www.yageo.com/upload/media/product/app/datasheet/rchip/pyu-rt_1-to-0.01_rohs_l.pdf | R_0402_1005_DensityHigh | 100 kOhms ±1% 0.063W, 1/16W Chip Resistor 0402 (1005 Metric) Thin Film | YAGEO | RT0402FRE07100KL | Digikey | YAG2307CT-ND
58 | 1 | SW1 | CAS-220TA | https://www.nidec-copal-electronics.com/e/catalog/switch/cas.pdf | CAS-220A_NDC-L | SWITCH SLIDE DPDT 100MA 6V | Nidec Components Corporation | CAS-220TA | Digikey | CAS220JCT-ND
59 | 1 | TH1 | 47k 1% NTC | https://www.murata.com/~/media/webrenewal/support/library/catalog/products/thermistor/r01e.ashx | R_0402_1005_DensityHigh | NTC Thermistor 47k 4050K 0402 (1005 Metric) | Murata Electronics | NCP15WB473F03RC | Digikey | 490-4802-1-ND
60 | 1 | U7 | AS5047P | https://ams.com/documents/20143/36005/AS5047P_DS000324_3-00.pdf | SOP-14_4.4x5mm_P0.65mm_H1.2mm | 14-Bit On-Axis Magnetic Rotary Position Sensor with 12-Bit Decimal and Binary Incremental Pulse Count for 28krpm High Speed Capability | ams-OSRAM USA INC. | AS5047P-ATSM | Digikey | AS5047P-ATSMCT-ND
61 | 1 | U8 | AS5048B | https://ams.com/documents/20143/36005/AS5048_DS000298_4-00.pdf | SOP-14_4.4x5mm_P0.65mm_H1.2mm | 14-bit Magnetic Rotary Encoder, I2C Interface | ams-OSRAM USA INC. | AS5048B-HTSP-500 | Digikey | AS5048B-HTSP-500CT-ND
62 | 1 | U11 | DGD0216WT-7 | https://www.diodes.com/assets/Datasheets/DGD0215-0216.pdf | SOT-23-5 | 1.9A HIGH SPEED SINGLE GATE DRIVER | Diodes Incorporated | DGD0216WT-7 | Digikey | DGD0216WT-7DICT-ND
63 | 1 | U6 | DRV8353FS | https://www.ti.com/lit/ds/symlink/drv8353f.pdf | WQFN-40-1EP_6x6mm_P0.5mm_EP4.15x4.15mm_ThermalVias | DRV835xF 100-V Three-Phase Smart Gate Driver | Texas Instruments | DRV8353FSRTAR | Digikey | 296-DRV8353FSRTARCT-ND
64 | 1 | U3 | LMR36006FSCQ | https://www.ti.com/lit/ds/symlink/lmr36006-q1.pdf | LMR36006 | LMR36006-Q1 4.2-V to 60-V, 0.6-A Ultra-Small Synchronous Step-Down Converter | Texas Instruments | LMR36006FSCQRNXTQ1 | Digikey | 296-LMR36006FSCQRNXTQ1CT-ND
65 | 1 | U2 | LMR36506MSC5RPERQ1 | https://www.ti.com/lit/ds/symlink/lmr36506-q1.pdf | LMR36503 | LMR36506-Q1 3-V to 65-V, 0.6-A Synchronous Buck Converter Optimized for Size and Light Load Efficiency | Texas Instruments | LMR36503MSC5RPERQ1 | Digikey | 296-LMR36506MSC5RPERQ1CT-ND
66 | 1 | U5 | LP2992IM5-3.3/NOPB | https://www.ti.com/lit/ds/symlink/lp2992.pdf | SOT95P280X145-5N | LP2992 Micropower 250-mA Low-Noise Ultra-Low-Dropout Regulator in SOT-23 and WSON Packages Designed for Use With Very Low-ESR Output Capacitors | Texas Instruments | LP2992IM5-3.3/NOPB | Digikey | LP2992IM5-3.3/NOPBCT-ND
67 | 1 | U9 | SN65HVD35DR | https://www.ti.com/lit/ds/symlink/sn65hvd30.pdf | SOIC-14 5.4mm | SN65HVD3x 3.3-V Full-Duplex RS-485 Drivers and Receivers | Texas Instruments | SN65HVD35DR | Digikey | 296-18706-1-ND
68 | 1 | U1 | STM32G474RET3 | https://www.st.com/resource/en/datasheet/stm32g474re.pdf | LQFP-64_10x10mm_P0.5mm | Arm® Cortex®-M4 32-bit MCU+FPU, 170 MHz / 213 DMIPS, 128 KB SRAM, rich analog, math acc, 184 ps 12 chan Hi-res timer | STMicroelectronics | STM32G474RET3 | Digikey | 497-STM32G474RET3-ND
69 | 1 | U10 | TCAN1051HGVDRBRQ1 | https://www.ti.com/general/docs/suppproductinfo.tsp?distId=10 | HVSON-8-1EP_3x3mm_P0.65mm_EP1.6x2.4mm_ThermalVias | TCAN1051-Q1 Automotive Fault Protected CAN Transceiver with CAN FD | Texas Instruments | TCAN1051HGVDRBRQ1 | Digikey | 296-TCAN1051HGVDRBRQ1CT-ND
70 | 1 | U4 | TPS62172DSG | http://www.ti.com/lit/ds/symlink/tps62170.pdf | WSON-8-1EP_2x2mm_P0.5mm_EP0.9x1.6mm_ThermalVias | TPS6217x 3-V to 17-V, 0.5-A Step-Down Converters with DCS-Control™ | Texas Instruments | TPS62172DSGR | Digikey | 296-39449-1-ND

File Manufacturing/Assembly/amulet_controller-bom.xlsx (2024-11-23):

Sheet: BoM
Bill of Materials
Schematic: | amulet_controller | Component Groups: | 71
Variant: | default | Component Count: | 253 (249 SMD/ 2 THT)
Revision: | 1.1 | Fitted Components: | 253 (249 SMD/ 2 THT)
Date: | 2024-04-13 | Number of PCBs: | 1
KiCad Version: | 8.0.6-8.0.6-0~ubuntu22.04.1 | Total Components: | 253
Row | Description | Part | References | Value | Footprint | Quantity Per PCB | Status | Datasheet | Supplier 1 | Supplier Part Number 1 | manf | manf# | Config
1 | 1000 pF ±10% 25V Ceramic Capacitor X7R 0402 (1005 Metric) | C_Small | C12 C13 C14 | 1n X7R 25V | C_0402_1005_DensityHigh | 3 |  | https://www.yageo.com/upload/media/product/app/datasheet/mlcc/upy-ac_np0x7rx7s_6_3v-to-2kv.pdf | Digikey | 311-3065-1-ND | YAGEO | AC0402KRX7R8BB102
2 | 3300 pF ±10% 100V Ceramic Capacitor X7R 0402 (1005 Metric) | C_Small | C133 C134 C135 C136 C137 C138 | 3n3 X7R 100V | C_0402_1005_DensityHigh | 6 |  | https://search.murata.co.jp/Ceramy/image/img/A01X/G101/ENG/GRM155R72A332KA01-01.pdf | Digikey | 490-8261-1-ND | Murata Electronics | GRM155R72A332KA01D | -NO_SNUBBER,-NONE
3 | 4700 pF ±10% 100V Ceramic Capacitor X7R 0402 (1005 Metric) | C_Small | C129 | 4n7 X7R 100V | C_0402_1005_DensityHigh | 1 |  | https://www.murata.com/-/media/webrenewal/support/library/catalog/products/k35e.ashx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 | Digikey | 490-4765-1-ND | Murata Electronics | GCM155R72A472KA37D
4 | 10000 pF ±10% 100V Ceramic Capacitor X7R 0402 (1005 Metric) | C_Small | C76 | 10n X7R 100V | C_0402_1005_DensityHigh | 1 |  | https://mm.digikey.com/Volume0/opasdata/d220001/medias/docus/2615/HMR105B7103KV-F_SS.pdf | Digikey | 587-HMR105B7103KV-FCT-ND | Taiyo Yuden | HMR105B7103KV-F
5 | 0.047 µF ±10% 100V Ceramic Capacitor X7R 0603 (1608 Metric) | C_Small | C91 | 47n X7R 100V | C_0603_1608_DensityHigh | 1 |  | https://connect.kemet.com:7667/gateway/IntelliData-ComponentDocumentation/1.0/download/datasheet/C0603C473K1RECAUTO | Digikey | 399-14764-1-ND | KEMET | C0603C473K1RECAUTO
6 | 0.1 µF ±10% 50V Ceramic Capacitor X7R 0402 (1005 Metric) | C_Small | C3 C4 C5 C8 C10 C11 C27 C28 C29 C101 C102 C103 C104 C105 C107 C108 C109 C111 C112 C113 C114 C115 C125 C126 C127 C128 | 100n X7R 50V | C_0402_1005_DensityHigh | 26 |  | https://search.murata.co.jp/Ceramy/image/img/A01X/G101/ENG/GCM155R71H104KE02-01.pdf | Digikey | 490-14514-1-ND | Murata Electronics | GCM155R71H104KE02J
7 | 0.1 µF ±10% 100V Ceramic Capacitor X7R 0603 (1608 Metric) | C | C22 C92 | 100n X7R 100V | C_0603_1608_DensityHigh | 2 |  | https://mm.digikey.com/Volume0/opasdata/d220001/medias/docus/21/HMK107B7104KAHT_SS.pdf | Digikey | 587-6009-1-ND | Taiyo Yuden | HMK107B7104KAHT
8 | 0.1 µF ±10% 16V Ceramic Capacitor X7R 0402 (1005 Metric) | C_Small | C90 | 100n X7R 16V | C_0402_1005_DensityHigh | 1 |  | https://search.murata.co.jp/Ceramy/image/img/A01X/G101/ENG/GCM155R71C104KA55-01.pdf | Digikey | 490-4759-1-ND | Murata Electronics | GCM155R71C104KA55D
9 | 0.1 µF ±10% 100V Ceramic Capacitor X7R 1206 (3216 Metric) | C_Small | C95 C97 C99 | 100n X7R 100V | C_1206_3216_DensityHighest | 3 |  | https://connect.kemet.com:7667/gateway/IntelliData-ComponentDocumentation/1.0/download/datasheet/C1206C104K1RACAUTO | Digikey | 399-7008-1-ND | KEMET | C1206C104K1RACAUTO
10 | 0.22 µF ±10% 100V Ceramic Capacitor X7S 0603 (1608 Metric) | C_Small | C23 C25 | 220n X7S 100V | C_0603_1608_DensityHigh | 2 |  | https://mm.digikey.com/Volume0/opasdata/d220001/medias/docus/2249/TMK105B7224KV-FR_SS.pdf | Digikey | 587-5012-1-ND | Taiyo Yuden | HMK107C7224KAHTE
11 | 1 µF ±10% 10V Ceramic Capacitor X7R 0402 (1005 Metric) | C | C2 C6 C9 C24 C26 | 1u X7R 10V | C_0402_1005_DensityHigh | 5 |  | https://search.murata.co.jp/Ceramy/image/img/A01X/G101/ENG/GRM155Z71A105KE01-01A.pdf | Digikey | 490-GRM155Z71A105KE01JCT-ND | Murata Electronics | GRM155Z71A105KE01J
12 | 1 µF ±10% 25V Ceramic Capacitor X7R 0603 (1608 Metric) | C | C60 C88 C93 | 1u X7R 25V | C_0603_1608_DensityHigh | 3 |  | https://mm.digikey.com/Volume0/opasdata/d220001/medias/docus/2146/TMK107AB7105KAHT_SS.pdf | Digikey | 587-3467-1-ND | Taiyo Yuden | TMK107AB7105KAHT
13 | 1 µF ±10% 6.3V Ceramic Capacitor X7R 0402 (1005 Metric) | C | C94 | 1u X7R 6.3V | C_0402_1005_DensityHigh | 1 |  | https://search.murata.co.jp/Ceramy/image/img/A01X/G101/ENG/GRT155R70J105KE01-01.pdf | Digikey | 490-18216-1-ND | Murata Electronics | GRT155R70J105KE01D
14 | Multilayer Ceramic Capacitors MLCC - SMD/SMT 0805 100VDC 2.2uF 10% 1.25mm AEC-Q200 | C | C15 C16 C17 C18 C20 C45 C52 | 2u2 X7R 100V | R_0805_2012_DensityHigh | 7 |  | https://product.tdk.com/system/files/dam/doc/product/capacitor/ceramic/mlcc/catalog/mlcc_automotive_midvoltage_en.pdf | Mouser | 810-CGA4J7R2A225K125 | TDK Corporation | CGA4J1X7R2A225K125AC
15 | 4.7 µF ±10% 16V Ceramic Capacitor X7R 0603 (1608 Metric) | C | C1 C84 C110 | 4u7 X7R 16V | C_0603_1608_DensityHigh | 3 |  | https://search.murata.co.jp/Ceramy/image/img/A01X/G101/ENG/GRM188Z71C475KE21-01A.pdf | Digikey | 490-GRM188Z71C475KE21JCT-ND | Murata Electronics | GRM188Z71C475KE21J
16 | 4.7 µF ±10% 100V Ceramic Capacitor X7R 1206 (3216 Metric) | C | C89 C96 C98 C100 | 4u7 X7R 100V | C_1206_3216_DensityHighest | 4 |  | https://search.murata.co.jp/Ceramy/image/img/A01X/G101/ENG/GRJ31CZ72A475KE01-01.pdf | Digikey | 490-GRJ31CZ72A475KE01LCT-ND | Murata Electronics | GRJ31CZ72A475KE01L
17 | 4.7 µF ±10% 100V Ceramic Capacitor X7R 1206 (3216 Metric) | C | C19 C21 C31 C32 C33 C34 C35 C36 C39 C40 C41 C42 C43 C44 C46 C47 C48 C49 C50 C51 C53 C54 C55 C57 C58 C59 C61 C62 C63 C64 C65 C66 C67 C68 C69 C70 C71 C72 C73 C74 C75 C77 C78 C79 C80 C81 C82 C85 C86 C87 | 4u7 X7R 100V | C_1206_3216_DensityHigh | 50 |  | https://search.murata.co.jp/Ceramy/image/img/A01X/G101/ENG/GRJ31CZ72A475KE01-01.pdf | Digikey | 490-GRJ31CZ72A475KE01LCT-ND | Murata Electronics | GRJ31CZ72A475KE01L
18 | 4.7 µF ±20% 25V Ceramic Capacitor X5R 0402 (1005 Metric) | C | C7 | 4u7 X5R 25V | C_0402_1005_DensityHigh | 1 |  | https://datasheets.kyocera-avx.com/cx5r.pdf | Digikey | 478-04023D475MAT2ACT-ND | KYOCERA AVX | 04023D475MAT2A
19 | 10 µF ±10% 25V Ceramic Capacitor X7R 0805 (2012 Metric) | C | C56 C106 | 10u X7R 25V | C_0805_2012_DensityHighest | 2 |  | https://search.murata.co.jp/Ceramy/image/img/A01X/G101/ENG/GRM21BZ71E106KE15-01.pdf | Digikey | 490-GRM21BZ71E106KE15LCT-ND | Murata Electronics | GRM21BZ71E106KE15L
20 | 15 µF ±20% 25V Ceramic Capacitor X7R 1210 (3225 Metric) | C | C30 C38 | 15u X7R 25V | C_1210_3225_DensityHigh | 2 |  | https://product.tdk.com/system/files/dam/doc/product/capacitor/ceramic/mlcc/catalog/mlcc_automotive_general_en.pdf | Digikey | 445-175431-1-ND | TDK Corporation | CGA6M3X7R1E156M200AB
21 | 22 µF ±20% 10V Ceramic Capacitor X7R 0805 (2012 Metric) | C | C37 C83 | 22u X7R 10V | C_0805_2012_DensityHighest | 2 |  | https://search.murata.co.jp/Ceramy/image/img/A01X/G101/ENG/GRM21BZ71A226ME15-01.pdf | Digikey | 490-GRM21BZ71A226ME15LCT-ND | Murata Electronics | GRM21BZ71A226ME15L
22 | 1000 pF ±10% 1000V (1kV) Ceramic Capacitor X7R 0603 (1608 Metric) | C_Small | C130 C131 C132 | 1n X7R 1kV | C_0603_1608_DensityHigh | 3 |  | https://connect.kemet.com:7667/gateway/IntelliData-ComponentDocumentation/1.0/download/specsheet/C0603V102KDRAC7867 | Digikey | 399-12306-1-ND | KEMET | C0603V102KDRAC7867
23 | Diode 100 V 200mA Surface Mount SOD-523 | BAT41KFILM | D3 D4 D5 D6 D7 D8 D9 D10 D11 D14 D15 D19 D20 D21 D22 | BAT41KFILM | D_SOD-523 | 15 |  | https://www.st.com/content/ccc/resource/technical/document/datasheet/5b/cd/d8/0a/45/56/41/6c/CD00130227.pdf/files/CD00130227.pdf/jcr:content/translations/en.C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 | Digikey | 497-5556-1-ND | STMicroelectronics | BAT41KFILM
24 | 26V, 14V Clamp 17A (8/20µs) Ipp Tvs Diode Surface Mount SOT-23-3 | CDSOT23-SM712 | D23 D27 | CDSOT23-SM712 | SOT95P230X110-3N | 2 |  | https://www.bourns.com/docs/Product-Datasheets/CDSOT23-SM712.pdf | Digikey | CDSOT23-SM712CT-ND | Bourns Inc. | CDSOT23-SM712
25 | Green 525nm LED Indication - Discrete 3V 1206 (3216 Metric) | LED | D13 | GREEN | LED_SM1206 | 1 |  | https://www.bivar.com/parts_content/Datasheets/SM1206NPGC-IL.pdf | Digikey | 492-1945-1-ND | Bivar Inc. | SM1206NPGC-IL
26 | 42V Clamp 2.6A (8/20µs) Ipp Tvs Diode Surface Mount SOT-323 | PESD2CANFD24V-UX | D24 D25 | PESD2CANFD24V-UX | SOT95P230X117-3N | 2 |  | https://assets.nexperia.com/documents/data-sheet/PESD2CANFD24V-U.pdf | Digikey | 1727-PESD2CANFD24V-UXCT-ND | Nexperia USA Inc. | PESD2CANFD24V-UX
27 | 3.5V (Typ) Clamp 7A (8/20µs) Ipp Tvs Diode Surface Mount, Wettable Flank DFN2510D-10 | PESD4USB3U-TBSX | D18 D26 | PESD4USB3U-TBSX | SOT1176D | 2 |  | https://assets.nexperia.com/documents/data-sheet/PESD4USB3U-TBS.pdf | Digikey | 1727-PESD4USB3U-TBSXCT-ND | Nexperia USA Inc. | PESD4USB3U-TBSX
28 | 5.5V (Typ) Clamp 7A (8/20µs) Ipp Tvs Diode Surface Mount, Wettable Flank DFN2510D-10 | PESD4USB5B-TBSX | D16 D17 | PESD4USB5B-TBSX | SOT1176D | 2 |  | https://assets.nexperia.com/documents/data-sheet/PESD4USB5B-TBS.pdf | Digikey | 1727-PESD4USB5B-TBSXCT-ND | Nexperia USA Inc. | PESD4USB5B-TBSX
29 | Surface-Mount TRANSZORB® Transient Voltage Suppressors | SMBJ51CD-M3/H | D1 D2 | SMBJ51CD-M3/H | DIOM4336X24N | 2 |  | https://www.vishay.com/docs/87606/smbj5cdthrusmbj120cd.pdf | Digikey | SMBJ51CD-M3/HGICT-ND | Vishay | SMBJ51CD-M3/H
30 | Yellow 592nm LED Indication - Discrete 2V 1206 (3216 Metric) | LED | D12 | YELLOW | LED_SM1206 | 1 |  | https://www.bivar.com/parts_content/Datasheets/SM1206NYC-IL.pdf | Digikey | 492-1947-1-ND | Bivar Inc. | SM1206NYC-IL
31 | 1 kOhms @ 100 MHz 1 Signal Line Ferrite Bead 0805 (2012 Metric) 1A 300mOhm | FerriteBead | FB1 FB2 FB3 FB4 | 1k @ 100MHz | R_0805_2012_DensityHigh | 4 |  | https://www.we-online.com/katalog/datasheet/742792096.pdf | Digikey | 732-4648-1-ND | Würth Elektronik | 742792096
32 | Connector Header Surface Mount, Right Angle 3 position 0.098" (2.50mm) | Conn_01x03 | J12 J13 | Nano-Fit 1x03 | 1054301203 | 2 |  | https://www.literature.molex.com/SQLImages/kelmscott/Molex/PDF_Images/987651-1223.PDF | Digikey | WM26098CT-ND | Molex | 1054301203
33 | Connector Header Surface Mount, Right Angle 2 position 0.079" (2.00mm) | Conn_01x02_Mounting | J8 J9 | S2B-PH-SM4-TB | JST_PH_S2B-PH-SM4-TB_1x02-1MP_P2.00mm_Horizontal | 2 |  | https://www.jst-mfg.com/product/pdf/eng/ePH.pdf | Digikey | 455-S2B-PH-SM4-TBCT-ND | JST Sales America Inc. | S2B-PH-SM4-TB
34 | Connector Header Surface Mount, Right Angle 5 position 0.049" (1.25mm) | Conn_01x05_Mounting | J14 | SM05B-GHS-TB | JST_GH_SM05B-GHS-TB_1x05-1MP_P1.25mm_Horizontal | 1 |  | https://www.jst-mfg.com/product/pdf/eng/eGH.pdf | Digikey | 455-SM05B-GHS-TBCT-ND | JST Sales America Inc. | SM05B-GHS-TB
35 | Connector Header Surface Mount, Right Angle 6 position 0.049" (1.25mm) | Conn_01x06_Mounting | J10 | SM06B-GHS-TB | JST_GH_SM06B-GHS-TB_1x06-1MP_P1.25mm_Horizontal | 1 |  | https://www.jst-mfg.com/product/pdf/eng/eGH.pdf | Digikey | 455-1568-1-ND | JST Sales America Inc. | SM06B-GHS-TB
36 | Connector Header Surface Mount, Right Angle 7 position 0.049" (1.25mm) | Conn_01x07_Mounting | J7 | SM07B-GHS-TB | JST_GH_SM07B-GHS-TB_1x07-1MP_P1.25mm_Horizontal | 1 |  | https://www.jst-mfg.com/product/pdf/eng/eGH.pdf | Digikey | 455-1569-1-ND | JST Sales America Inc. | SM07B-GHS-TB(LF)(SN)
37 | Connector Header Surface Mount, Right Angle 8 position 0.049" (1.25mm) | Conn_01x08_Mounting | J6 | SM08B-GHS-TB | JST_GH_SM08B-GHS-TB_1x08-1MP_P1.25mm_Horizontal | 1 |  | https://www.jst-mfg.com/product/pdf/eng/eGH.pdf | Digikey | 455-1570-1-ND | JST Sales America Inc. | SM08B-GHS-TB
38 | Socket; DC supply; XT60; female; PIN: 2; on PCBs; THT; yellow; 30A | Conn_01x02_Mounting | J1 | XT60PW-F | AMASS_XT60PW-F_1x02_P7.20mm_Horizontal | 1 |  | https://www.tme.eu/Document/1191bc2fa3aee3c446e5a895fd8f7983/XT60PW-F.pdf | Transfer Multisort Elektronik | XT60PW-F | AMASS | XT60PW-F | -NO_XT60,-NONE
39 | Socket; DC supply; XT60; male; PIN: 2; on PCBs; THT; yellow; 30A; 500V | Conn_01x02_Mounting | J2 | XT60PW-M | AMASS_XT60PW-M_1x02_P7.20mm_Horizontal | 1 |  | https://www.tme.eu/Document/b13629717d44ae038681dba08d18c0b6/XT60PW-M.pdf | Transfer Multisort Elektronik | XT60PW-M | AMASS | XT60PW-M | -NO_XT60,-NONE
40 | Power Inductors - SMD 2.2uH Shld 20% 1.2A 100 mOhms | L | L3 | 2u2 | L_Coilcraft_LPS3314 | 1 |  | https://www.coilcraft.com/getmedia/3ba581dc-6d87-4be6-9dea-9167ac97554d/lps3314.pdf | Mouser | 994-LPS3314-222MRC | Coilcraft | LPS3314-222MRC
41 | Power Inductors - SMD 22uH Shld 20% 830mA 360 mOhms | L | L1 L2 | 22u | L_Coilcraft_LPS4018 | 2 |  | https://www.coilcraft.com/getmedia/31b05c96-4c4c-4498-8dbb-fe092de76bad/lps4018.pdf | Mouser | 994-LPS4018-223MRC | Coilcraft | LPS4018-223MRC
42 | N-Channel 30 V 3A (Ta) 460mW (Ta) Surface Mount TO-236AB | PMV90ENER | Q7 Q8 Q9 | PMV90ENER | SOT-23-3 | 3 |  | https://assets.nexperia.com/documents/data-sheet/PMV90ENE.pdf | Digikey | 1727-2735-1-ND | Nexperia USA Inc. | PMV90ENER
43 | N-Channel 60 V 260A (Tc) 960mW (Ta), 170W (Tc) Surface Mount 8-DSOP Advance | TPW1R306PL,L1Q | Q1 Q2 Q3 Q4 Q5 Q6 | TPW1R306PL,L1Q | 2-5S1A | 6 |  | https://toshiba.semicon-storage.com/info/TPW1R306PL_datasheet_en_20191021.pdf?did=55843&prodName=TPW1R306PL | Digikey | TPW1R306PLL1QCT-ND | Toshiba Semiconductor and Storage | TPW1R306PL,L1Q
44 | 0.5 mOhms ±1% 2W Chip Resistor 1206 (3216 Metric) Automotive AEC-Q200, Current Sense, Moisture Resistant Metal Element | R_Small | R12 R15 R18 | 0m5 1% 2W | HCS1206FTL500 | 3 |  | https://www.seielect.com/catalog/sei-hcs.pdf | Digikey | HCS1206FTL500CT-ND | Stackpole Electronics Inc | HCS1206FTL500
45 | 0 Ohms Jumper Chip Resistor 0402 (1005 Metric) Automotive AEC-Q200 Thick Film | R | R4 R31 R32 | 0R | R_0402_1005_DensityHigh | 3 |  | https://industrial.panasonic.com/ww/products/pt/general-purpose-chip-resistors/models/ERJ2GE0R00X | Digikey | P0.0JCT-ND | Panasonic Electronic Components | ERJ-2GE0R00X
46 | 0 Ohms Jumper Chip Resistor 0603 (1608 Metric) Automotive AEC-Q200, Pulse Withstanding Thick Film | R_Small | R53 | 0R | R_0603_1608_DensityHigh | 1 |  | https://www.vishay.com/docs/20043/crcwhpe3.pdf | Digikey | 541-0.0SBCT-ND | Vishay | CRCW06030000Z0EAHP
47 | 5 Ohms ±1% 0.4W Chip Resistor 0603 (1608 Metric) Automotive AEC-Q200, Current Sense Thin Film | R_Small | R55 R56 R57 R58 R59 R60 | 5R 1% 0.4W | R_0603_1608_DensityHigh | 6 |  | https://www.seielect.com/catalog/sei-csrt.pdf | Digikey | 738-CSRT0603FT5R00CT-ND | Stackpole Electronics Inc | CSRT0603FT5R00 | -NO_SNUBBER,-NONE
48 | 7.5 Ohms ±1% 0.5W, 1/2W Chip Resistor 0805 (2012 Metric) Automotive AEC-Q200, Pulse Withstanding Thick Film | R_Small | R10 R11 R13 R14 R16 R17 | 7R5 1% 1/2W | R_0805_2012_DensityHigh | 6 |  | https://www.vishay.com/docs/20043/crcwhpe3.pdf | Digikey | 541-7.50TCT-ND | Vishay | CRCW08057R50FKEAHP
49 | 10 Ohms ±1% 0.333W, 1/3W Chip Resistor 0603 (1608 Metric) Automotive AEC-Q200, Pulse Withstanding Thick Film | R_Small | R34 | 10R 1% | R_0603_1608_DensityHigh | 1 |  | https://www.vishay.com/docs/20043/crcwhpe3.pdf | Digikey | 541-10.0SCT-ND | Vishay | CRCW060310R0FKEAHP
50 | 22 Ohms ±1% 0.1W, 1/10W Chip Resistor 0402 (1005 Metric) Automotive AEC-Q200 Thick Film | R_Small | R1 R2 R3 | 22R 1% | R_0402_1005_DensityHigh | 3 |  | https://industrial.panasonic.com/cdbs/www-data/pdf/RDA0000/AOA0000C304.pdf | Digikey | P22.0LCT-ND | Panasonic Electronic Components | ERJ-2RKF22R0X
51 | 60.4 Ohms ±1% 0.25W, 1/4W Chip Resistor 0603 (1608 Metric) Automotive AEC-Q200, Pulse Withstanding Thick Film | R_Small | R50 R51 | 60R4 1% 1/4W | R_0603_1608_DensityHigh | 2 |  | https://www.rohm.com/datasheet?p=ESR01MZPF&dist=Digi-key&media=referral&campaign=Digi-key | Digikey | 511-ESR03EZPF60R4CT-ND | Rohm Semiconductor | ESR03EZPF60R4
52 | 100 Ohms ±1% 0.2W, 1/5W Chip Resistor 0402 (1005 Metric) Automotive AEC-Q200, Pulse Withstanding Thick Film | R_Small | R22 R23 R25 R35 R36 R37 R38 R39 R40 R41 R42 R43 R48 R49 | 100R 1% 1/5W | R_0402_1005_DensityHigh | 14 |  | https://www.vishay.com/docs/20065/rcse3.pdf | Digikey | 541-2886-1-ND | Vishay | RCS0402100RFKED
53 | 150 Ohms ±1% 0.2W, 1/5W Chip Resistor 0402 (1005 Metric) Automotive AEC-Q200, Pulse Withstanding Thick Film | R_Small | R26 | 150R 1% 1/5W | R_0402_1005_DensityHigh | 1 |  | https://www.vishay.com/docs/20043/crcwhpe3.pdf | Digikey | 541-150YCT-ND | Vishay | CRCW0402150RFKEDHP
54 | 2 kOhms ±1% 0.1W, 1/10W Chip Resistor 0402 (1005 Metric) Automotive AEC-Q200 Thick Film | R | R8 R9 R28 R44 R45 R46 R47 | 2k 1% | R_0402_1005_DensityHigh | 7 |  | https://industrial.panasonic.com/cdbs/www-data/pdf/RDA0000/AOA0000C304.pdf | Digikey | P2.00KLCT-ND | Vishay | ERJ-2RKF2001X
55 | 4.7 kOhms ±1% 0.063W, 1/16W Chip Resistor 0402 (1005 Metric) Moisture Resistant Thin Film | R | R30 | 4k7 1% | R_0402_1005_DensityHigh | 1 |  | https://www.yageo.com/upload/media/product/app/datasheet/rchip/pyu-rt_1-to-0.01_rohs_l.pdf | Digikey | 13-RT0402FRE134K7LCT-ND | YAGEO | RT0402FRE134K7L
56 | 9.09 kOhms ±1% 0.063W, 1/16W Chip Resistor 0402 (1005 Metric) Thin Film | R | R6 | 9k09 1% | R_0402_1005_DensityHigh | 1 |  | https://www.yageo.com/upload/media/product/app/datasheet/rchip/pyu-rt_1-to-0.01_rohs_l.pdf | Digikey | 13-RT0402FRE079K09LCT-ND | YAGEO | RT0402FRE079K09L
57 | 10 kOhms ±1% 0.063W, 1/16W Chip Resistor 0402 (1005 Metric) Thin Film | R | R7 R27 R33 | 10k 1% | R_0402_1005_DensityHigh | 3 |  | https://www.yageo.com/upload/media/product/app/datasheet/rchip/pyu-rt_1-to-0.01_rohs_l.pdf | Digikey | YAG1233CT-ND | YAGEO | RT0402FRE0710KL
58 | 100 kOhms ±1% 0.063W, 1/16W Chip Resistor 0402 (1005 Metric) Thin Film | R | R5 R19 R20 R21 R24 R29 | 100k 1% | R_0402_1005_DensityHigh | 6 |  | https://www.yageo.com/upload/media/product/app/datasheet/rchip/pyu-rt_1-to-0.01_rohs_l.pdf | Digikey | YAG2307CT-ND | YAGEO | RT0402FRE07100KL
59 | SWITCH SLIDE DPDT 100MA 6V | SW_DPDT_x2 | SW1 | CAS-220TA | CAS-220A_NDC-L | 1 |  | https://www.nidec-copal-electronics.com/e/catalog/switch/cas.pdf | Digikey | CAS220JCT-ND | Nidec Components Corporation | CAS-220TA
60 | NTC Thermistor 47k 4050K 0402 (1005 Metric) | Thermistor_NTC | TH1 | 47k 1% NTC | R_0402_1005_DensityHigh | 1 |  | https://www.murata.com/~/media/webrenewal/support/library/catalog/products/thermistor/r01e.ashx | Digikey | 490-4802-1-ND | Murata Electronics | NCP15WB473F03RC
61 | 14-Bit On-Axis Magnetic Rotary Position Sensor with 12-Bit Decimal and Binary Incremental Pulse Count for 28krpm High Speed Capability | AS5047P | U7 | AS5047P | SOP-14_4.4x5mm_P0.65mm_H1.2mm | 1 |  | https://ams.com/documents/20143/36005/AS5047P_DS000324_3-00.pdf | Digikey | AS5047P-ATSMCT-ND | ams-OSRAM USA INC. | AS5047P-ATSM
62 | 14-bit Magnetic Rotary Encoder, I2C Interface | AS5048B | U8 | AS5048B | SOP-14_4.4x5mm_P0.65mm_H1.2mm | 1 |  | https://ams.com/documents/20143/36005/AS5048_DS000298_4-00.pdf | Digikey | AS5048B-HTSP-500CT-ND | ams-OSRAM USA INC. | AS5048B-HTSP-500
63 | 1.9A HIGH SPEED SINGLE GATE DRIVER | DGD0216WT-7 | U11 | DGD0216WT-7 | SOT-23-5 | 1 |  | https://www.diodes.com/assets/Datasheets/DGD0215-0216.pdf | Digikey | DGD0216WT-7DICT-ND | Diodes Incorporated | DGD0216WT-7
64 | DRV835xF 100-V Three-Phase Smart Gate Driver | DRV8353FS | U6 | DRV8353FS | WQFN-40-1EP_6x6mm_P0.5mm_EP4.15x4.15mm_ThermalVias | 1 |  | https://www.ti.com/lit/ds/symlink/drv8353f.pdf | Digikey | 296-DRV8353FSRTARCT-ND | Texas Instruments | DRV8353FSRTAR
65 | LMR36006-Q1 4.2-V to 60-V, 0.6-A Ultra-Small Synchronous Step-Down Converter | LMR36006FSCQ | U3 | LMR36006FSCQ | LMR36006 | 1 |  | https://www.ti.com/lit/ds/symlink/lmr36006-q1.pdf | Digikey | 296-LMR36006FSCQRNXTQ1CT-ND | Texas Instruments | LMR36006FSCQRNXTQ1
66 | LMR36506-Q1 3-V to 65-V, 0.6-A Synchronous Buck Converter Optimized for Size and Light Load Efficiency | LMR36506MSC5RPERQ1 | U2 | LMR36506MSC5RPERQ1 | LMR36503 | 1 |  | https://www.ti.com/lit/ds/symlink/lmr36506-q1.pdf | Digikey | 296-LMR36506MSC5RPERQ1CT-ND | Texas Instruments | LMR36503MSC5RPERQ1
67 | LP2992 Micropower 250-mA Low-Noise Ultra-Low-Dropout Regulator in SOT-23 and WSON Packages Designed for Use With Very Low-ESR Output Capacitors | LP2992IM5-3.3/NOPB | U5 | LP2992IM5-3.3/NOPB | SOT95P280X145-5N | 1 |  | https://www.ti.com/lit/ds/symlink/lp2992.pdf | Digikey | LP2992IM5-3.3/NOPBCT-ND | Texas Instruments | LP2992IM5-3.3/NOPB
68 | SN65HVD3x 3.3-V Full-Duplex RS-485 Drivers and Receivers | SN65HVD35DR | U9 | SN65HVD35DR | SOIC-14 5.4mm | 1 |  | https://www.ti.com/lit/ds/symlink/sn65hvd30.pdf | Digikey | 296-18706-1-ND | Texas Instruments | SN65HVD35DR
69 | Arm® Cortex®-M4 32-bit MCU+FPU, 170 MHz / 213 DMIPS, 128 KB SRAM, rich analog, math acc, 184 ps 12 chan Hi-res timer | STM32G474RETx | U1 | STM32G474RET3 | LQFP-64_10x10mm_P0.5mm | 1 |  | https://www.st.com/resource/en/datasheet/stm32g474re.pdf | Digikey | 497-STM32G474RET3-ND | STMicroelectronics | STM32G474RET3
70 | TCAN1051-Q1 Automotive Fault Protected CAN Transceiver with CAN FD | TCAN1051HGVDRBRQ1 | U10 | TCAN1051HGVDRBRQ1 | HVSON-8-1EP_3x3mm_P0.65mm_EP1.6x2.4mm_ThermalVias | 1 |  | https://www.ti.com/general/docs/suppproductinfo.tsp?distId=10 | Digikey | 296-TCAN1051HGVDRBRQ1CT-ND | Texas Instruments | TCAN1051HGVDRBRQ1
71 | TPS6217x 3-V to 17-V, 0.5-A Step-Down Converters with DCS-Control™ | TPS62172DSG | U4 | TPS62172DSG | WSON-8-1EP_2x2mm_P0.5mm_EP0.9x1.6mm_ThermalVias | 1 |  | http://www.ti.com/lit/ds/symlink/tps62170.pdf | Digikey | 296-39449-1-ND | Texas Instruments | TPS62172DSGR
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

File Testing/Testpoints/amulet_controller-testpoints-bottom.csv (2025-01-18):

Ref. | Net | X [mm] | Y [mm]
TP7 | DRV_CS | 31.90 | 20.10
TP23 | POS_SENSOR_CS | 31.05 | 19.25
TP29 | RS422_~{RE} | 29.63 | 17.71
TP30 | RS422_DE | 27.65 | 15.20
TP35 | FAN_CTRL | 36.84 | 12.79
TP36 | SENSE_TEMP_MOT | 30.31 | 11.52
TP44 | F_VIN_3V3 | 14.15 | 33.25
TP47 | +5V | 56.61 | 24.08
TP50 | +3V3 | 57.68 | 25.69
TP58 | GND | 58.25 | 27.56
TP74 | FAN_SW | 36.70 | 7.35

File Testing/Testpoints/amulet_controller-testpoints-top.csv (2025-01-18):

Ref. | Net | X [mm] | Y [mm]
TP1 | MOTOR_ENABLE | 40.58 | 22.69
TP2 | MOTOR_HIZ | 37.88 | 26.50
TP3 | MOTOR_FAULT | 32.78 | 25.46
TP4 | DRV_SCLK | 35.77 | 25.38
TP5 | DRV_MISO | 34.17 | 24.75
TP6 | DRV_MOSI | 41.36 | 21.98
TP8 | PWM_PHASEA | 38.40 | 24.35
TP9 | PWM_PHASEB | 39.05 | 23.37
TP10 | PWM_PHASEC | 39.65 | 24.35
TP11 | SOA | 30.28 | 25.30
TP12 | SOB | 29.58 | 24.60
TP13 | SOC | 28.88 | 23.90
TP14 | SWDIO | 45.53 | 15.02
TP15 | SWCLK | 44.60 | 14.45
TP16 | NRST | 44.60 | 15.60
TP17 | AUX1_A | 51.55 | 28.11
TP18 | AUX1_B | 51.19 | 29.89
TP19 | AUX1_C | 51.02 | 31.02
TP20 | AUX1_D | 52.47 | 31.42
TP21 | AUX1_E | 52.86 | 33.02
TP22 | AUX1_I2C_PULLUP | 41.70 | 8.80
TP24 | AUX2_A | 21.70 | 26.10
TP25 | AUX2_B | 21.70 | 25.20
TP26 | AUX2_C | 20.80 | 25.20
TP27 | AUX2_D | 20.80 | 24.30
TP28 | AUX2_I2C_PULLUP | 27.70 | 9.30
TP31 | LED_DBG | 26.55 | 8.15
TP32 | LED_PWR | 27.70 | 8.15
TP33 | FDCAN_RX | 54.50 | 35.20
TP34 | FDCAN_TX | 53.59 | 34.64
TP37 | SENSE_TEMP_FET | 13.34 | 47.28
TP38 | SENSE_VBAT | 12.67 | 35.77
TP39 | +VBAT | 8.78 | 45.85
TP40 | +VBAT | 43.95 | 33.50
TP41 | +VBAT | 14.50 | 37.80
TP42 | F_VIN_12V | 48.05 | 31.75
TP43 | F_VIN_5V | 11.40 | 39.15
TP45 | +12V | 46.01 | 16.53
TP46 | +5V | 5.75 | 44.05
TP48 | +3V3 | 17.52 | 24.28
TP49 | +3V3 | 43.60 | 14.00
TP51 | +A3V3 | 26.80 | 29.72
TP52 | GND | 31.17 | 26.25
TP53 | GND | 56.95 | 39.22
TP54 | GND | 43.45 | 11.80
TP55 | GND | 17.68 | 35.27
TP56 | GND | 51.12 | 23.25
TP57 | GND | 45.53 | 13.90
TP59 | GHA | 43.58 | 34.55
TP60 | GLA | 43.58 | 35.75
TP61 | SHA | 44.00 | 35.15
TP62 | GHB | 30.42 | 35.38
TP63 | GLB | 32.07 | 35.58
TP64 | SHB | 30.57 | 36.08
TP65 | GHC | 26.27 | 35.88
TP66 | GLC | 26.27 | 34.50
TP67 | SHC | 25.77 | 35.27
TP68 | SA_P | 36.22 | 34.74
TP69 | SA_N | 35.47 | 34.74
TP70 | SB_P | 33.65 | 34.93
TP71 | SB_N | 34.40 | 34.93
TP72 | SC_P | 30.21 | 31.65
TP73 | SC_N | 30.21 | 30.90

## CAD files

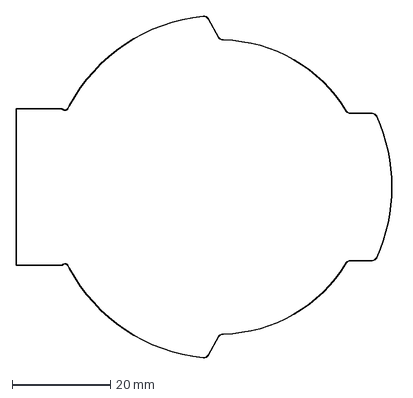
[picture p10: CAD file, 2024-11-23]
DXF_SVG/outline.dxf
77.7 x 69.7 mm

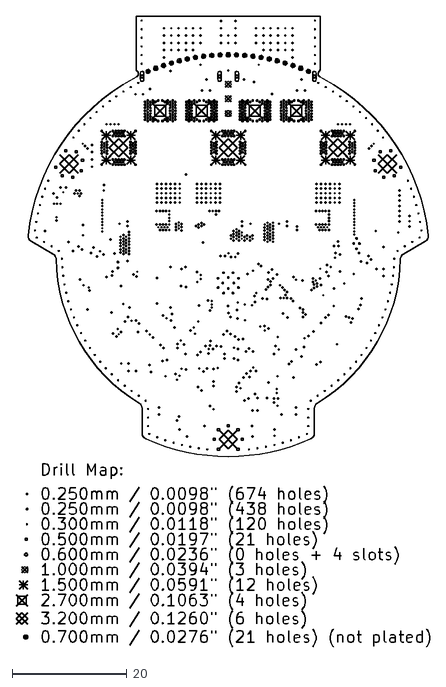
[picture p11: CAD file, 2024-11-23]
Manufacturing/Fabrication/Gerbers/amulet_controller-drill_map.dxf
72.0 x 109.8

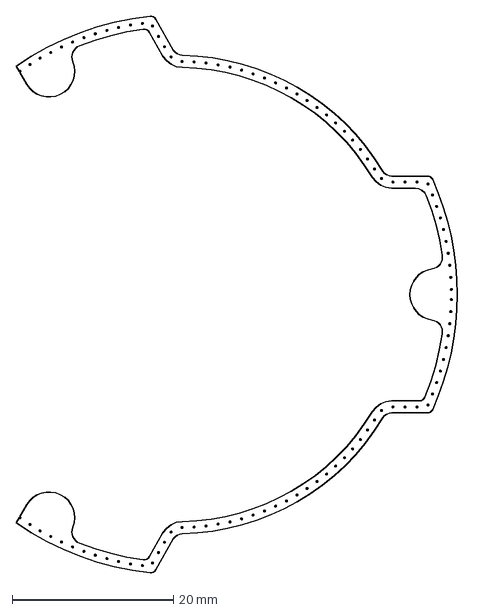
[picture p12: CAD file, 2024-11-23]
DXF_SVG/guard_ring_vias.dxf
55.8 x 69.1 mm

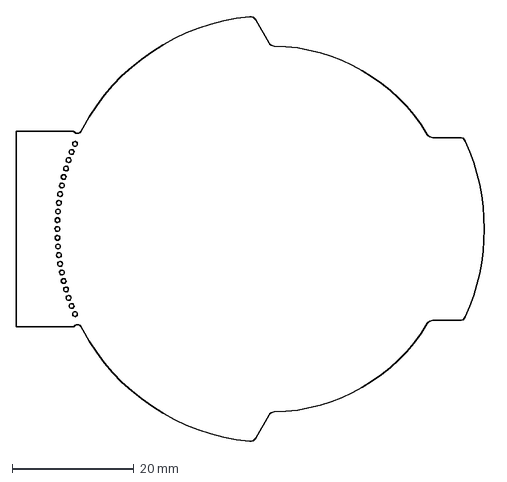
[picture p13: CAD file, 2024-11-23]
DXF_SVG/breakoff-mousebites.dxf
77.7 x 69.7 mm

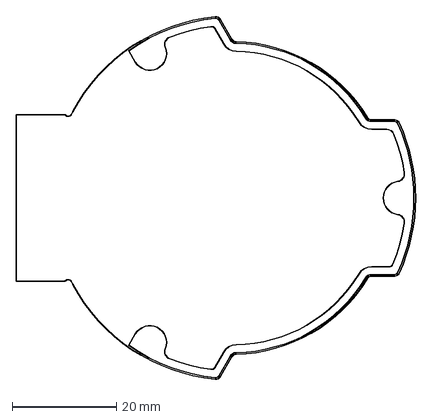
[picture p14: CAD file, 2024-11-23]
DXF_SVG/guard_ring.dxf
77.7 x 69.7 mm

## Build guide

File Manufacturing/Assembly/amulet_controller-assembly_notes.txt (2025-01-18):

ASSEMBLY NOTES (UNLESS OTHERWISE SPECIFIED)

1)	DO NOT POPULATE PARTS ARE MARKED WITH A RED CROSS.

2)	DO NOT POPULATE PARTS ARE NOT PRESENT IN THE BOM.

3)	IF CONFLICTING INFORMATION IS FOUND BETWEEN THE ASSEMBLY
	FILE AND BOM, BOM SHOULD BE USED AS THE MAIN SOURCE.

4)	CONFORMAL COATING IS NOT REQUIRED.

5)	DOT IDENTIFIES PIN #1 LOCATION AND DEVICE ORIENTATION
	WHEN VIEWED FROM THE TOP.

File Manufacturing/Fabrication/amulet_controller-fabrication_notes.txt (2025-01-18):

FABRICATION NOTES (UNLESS OTHERWISE SPECIFIED)

1)	FABRICATE PER IPC-6012A CLASS 2.

2)	OUTLINE DEFINED IN SEPARATE GERBER FILE WITH
	"Edge_Cuts.GBR" SUFFIX.

	DIMENSIONS OF CIRCUMSIZED RECTANGLE SHOWN ON THIS
	DRAWING FOR REFERENCE ONLY.

3)	SEE SEPARATE DRILL FILES WITH ".DRL" SUFFIX 
	FOR HOLE LOCATIONS.

	SELECTED HOLE LOCATIONS SHOWN ON THIS DRAWING 
	FOR REFERENCE ONLY.

4)	SURFACE FINISH: IMMERSION GOLD

5)	SOLDERMASK ON BOTH SIDES OF THE BOARD SHALL 
	BE LPI, COLOR BLACK.

6)	SILK SCREEN LEGEND TO BE APPLIED PER LAYER 
	STACKUP USING YELLOW NON-CONDUCTIVE EPOXY INK.

7)	ALL VIAS ARE TENTED ON BOTH SIDES UNLESS 
	SOLDERMASK OPENED IN GERBER.

8)	VENDOR SHOULD FOLLOW ROHS COMPLIANT PROCESS 
	AND Pb FREE FOR MANUFACTURING

9)	PCB MATERIAL REQUIREMENTS:

	A.	FLAMMABILITY RATING MUST MEET OR EXCEED 
		UL94V-0 REQUIREMENTS.
	B.	Tg 170 C OR EQUIVALENT.
	C.	EQUIVALENT MATERIAL SHALL BE RoHS COMPLIANT, 
		HALOGEN FREE AND APPROVED BY EPFL XPLORE RESEARCH.

10)	DESIGN GEOMETRY MINIMUM FEATURE SIZES:

	BOARD SIZE				69.666 × 76.700 mm
	BOARD THICKNESS		1.660 mm
	TRACE WIDTH			0.200 mm
	TRACE TO TRACE		0.200 mm
	MIN. HOLE (PTH)			0.250 mm
	MIN. HOLE (NPTH)		0.700 mm
	ANNULAR RING			0.150 mm
	COPPER TO HOLE		0.254 mm
	COPPER TO EDGE		0.250 mm
	HOLE TO HOLE			0.254 mm

11)	REFER TO IMPEDANCE TABLE FOR IMPEDANCE CONTROL REQUIREMENTS.

12)	CONFIRM SPACE WIDTHS AND SPACINGS.

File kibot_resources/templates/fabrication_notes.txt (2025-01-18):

FABRICATION NOTES (UNLESS OTHERWISE SPECIFIED)

1)	FABRICATE PER IPC-6012A CLASS 2.

2)	OUTLINE DEFINED IN SEPARATE GERBER FILE WITH
	"Edge_Cuts.GBR" SUFFIX.

	DIMENSIONS OF CIRCUMSIZED RECTANGLE SHOWN ON THIS
	DRAWING FOR REFERENCE ONLY.

3)	SEE SEPARATE DRILL FILES WITH ".DRL" SUFFIX 
	FOR HOLE LOCATIONS.

	SELECTED HOLE LOCATIONS SHOWN ON THIS DRAWING 
	FOR REFERENCE ONLY.

4)	SURFACE FINISH: ${pcb_finish_cap}

5)	SOLDERMASK ON BOTH SIDES OF THE BOARD SHALL 
	BE LPI, COLOR ${solder_mask_color_text_cap}.

6)	SILK SCREEN LEGEND TO BE APPLIED PER LAYER 
	STACKUP USING ${silk_screen_color_text_cap} NON-CONDUCTIVE EPOXY INK.

7)	ALL VIAS ARE TENTED ON BOTH SIDES UNLESS 
	SOLDERMASK OPENED IN GERBER.

8)	VENDOR SHOULD FOLLOW ROHS COMPLIANT PROCESS 
	AND Pb FREE FOR MANUFACTURING

9)	PCB MATERIAL REQUIREMENTS:

	A.	FLAMMABILITY RATING MUST MEET OR EXCEED 
		UL94V-0 REQUIREMENTS.
	B.	Tg 170 C OR EQUIVALENT.
	C.	EQUIVALENT MATERIAL SHALL BE RoHS COMPLIANT, 
		HALOGEN FREE AND APPROVED BY ${COMPANY_cap}.

10)	DESIGN GEOMETRY MINIMUM FEATURE SIZES:

	BOARD SIZE				${bb_w_mm} × ${bb_h_mm} mm
	BOARD THICKNESS		${thickness_mm} mm
	TRACE WIDTH			${track_mm} mm
	TRACE TO TRACE		${clearance_mm} mm
	MIN. HOLE (PTH)			${drill_pth_real_mm} mm
	MIN. HOLE (NPTH)		${drill_npth_real_mm} mm
	ANNULAR RING			${oar_mm} mm
	COPPER TO HOLE		${c2h_mm} mm
	COPPER TO EDGE		${c2e_mm} mm
	HOLE TO HOLE			${h2h_mm} mm
#?stackup and impedance_controlled

#?stackup and impedance_controlled
11)	REFER TO IMPEDANCE TABLE FOR IMPEDANCE CONTROL REQUIREMENTS.
#?stackup and impedance_controlled

#?stackup and impedance_controlled
12)	CONFIRM SPACE WIDTHS AND SPACINGS.

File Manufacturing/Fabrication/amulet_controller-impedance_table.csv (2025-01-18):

Transmission Line | Impedance [ohms] | Tolerance [ohms] | Layer | Trace Width [mm] | Gap [mm] | Ref. Layers
Edge-Coupled Coated Microstrip | 100 | ±10 % | L1 | 0.2032 | 0.28 | L2

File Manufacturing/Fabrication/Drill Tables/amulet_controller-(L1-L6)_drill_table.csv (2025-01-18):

Count | Hole Size | Plated | Hole Shape | Drill Layer Pair | Hole Type
674 | 0.25mm (9.84mils) | PTH | Round | L1 (Sig, PWR) - L6 (Sig, PWR) | Via
438 | 0.25mm (9.84mils) | PTH | Round | L1 (Sig, PWR) - L6 (Sig, PWR) | Pad
120 | 0.30mm (11.81mils) | PTH | Round | L1 (Sig, PWR) - L6 (Sig, PWR) | Via
21 | 0.50mm (19.69mils) | PTH | Round | L1 (Sig, PWR) - L6 (Sig, PWR) | Pad
4 | 0.60mm (23.62mils) | PTH | Slot | L1 (Sig, PWR) - L6 (Sig, PWR) | Pad
3 | 1.00mm (39.37mils) | PTH | Round | L1 (Sig, PWR) - L6 (Sig, PWR) | Pad
12 | 1.50mm (59.06mils) | PTH | Round | L1 (Sig, PWR) - L6 (Sig, PWR) | Pad
4 | 2.70mm (106.30mils) | PTH | Round | L1 (Sig, PWR) - L6 (Sig, PWR) | Pad
6 | 3.20mm (125.98mils) | PTH | Round | L1 (Sig, PWR) - L6 (Sig, PWR) | Pad
Total 1282

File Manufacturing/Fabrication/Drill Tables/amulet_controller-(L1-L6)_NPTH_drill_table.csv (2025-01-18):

Count | Hole Size | Plated | Hole Shape | Drill Layer Pair | Hole Type
21 | 0.70mm (27.56mils) | NPTH | Round | L1 (Sig, PWR) - L6 (Sig, PWR) | Mechanical
Total 21

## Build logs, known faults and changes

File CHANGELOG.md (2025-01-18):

# Changelog

## [Unreleased]

## [1.1.1] - 2025-01-18

### Fixed

-   Replace non-stocked components. 

## [1.1.0] - 2024-04-13

### Added

-   RC snubber passive values.

### Fixed

-   More vias for VBUS and LMR36006 GND pads.
-   Board version voltage reference from +3V3 to +A3V3.

### Changed

-   Motor thermistor resistor divider to 2kOhm for a 10k 3950K thermistor.

## [1.0.2] - 2024-03-12

### Changed

-   Power sequencing graph according to experimental data.

## [1.0.1] - 2024-01-25

### Added

-   Controller target specifications.
-   Credits to moteus on cover page.
-   Optional RC-Snubber to power stage.

### Fixed

-   Chassis guard ring to go around the board.
-   CAN and power TVS diodes now go to chassis.
-   Clearance between nets to respect IEC60664-1 where possible.
-   Comment on precharge.
-   Power TVS diode reference designator from "U" to "D".

### Changed

-   5V 300 mA buck converter with 600 mA version.
-   Chassis-GND capacitor by 1nF 1kV.

## [1.0.0] - 2023-12-12

### Added

-   TVS protection and termination switch to FD-CAN.
-   Low-side switched 12V 600 mA source for external fan.
-   LDO for analog supply.
-   One TVS diode per power connector.
-   Second on-board I2C magnetic encoder for disambiguation.
-   ESD protection to all interfaces.
-   Over-voltage protection on thermistor ADC inputs.
-   Pi filters to inputs of buck regulators and MCU analog supply.
-   Decoupling caps next to power pins of connectors.

### Changed

-   CPH-CPL capacitor to 47 nF (gate driver).
-   FD-CAN transceiver IC.
-   FETs for top cooled variant.
-   Input power TVS diode to bidirectional.
-   Moved SOx low-pass filter to MCU section.
-   PWM_PHASEA with PWM_PHASEC on STM32G474 pinout for easier routing.
-   RS422 pinout on connector.
-   Buck regulators to optimize for low noise.

[Unreleased]: https://github.com/nguyen-v/amulet_controller_kibot/compare/1.1.1...HEAD

[1.1.1]: https://github.com/nguyen-v/amulet_controller_kibot/compare/1.1.1...1.1.1

[1.1.1]: https://github.com/nguyen-v/amulet_controller_kibot/compare/75a4252278e2e99f125718f921b713f39e2bfcda...1.1.1

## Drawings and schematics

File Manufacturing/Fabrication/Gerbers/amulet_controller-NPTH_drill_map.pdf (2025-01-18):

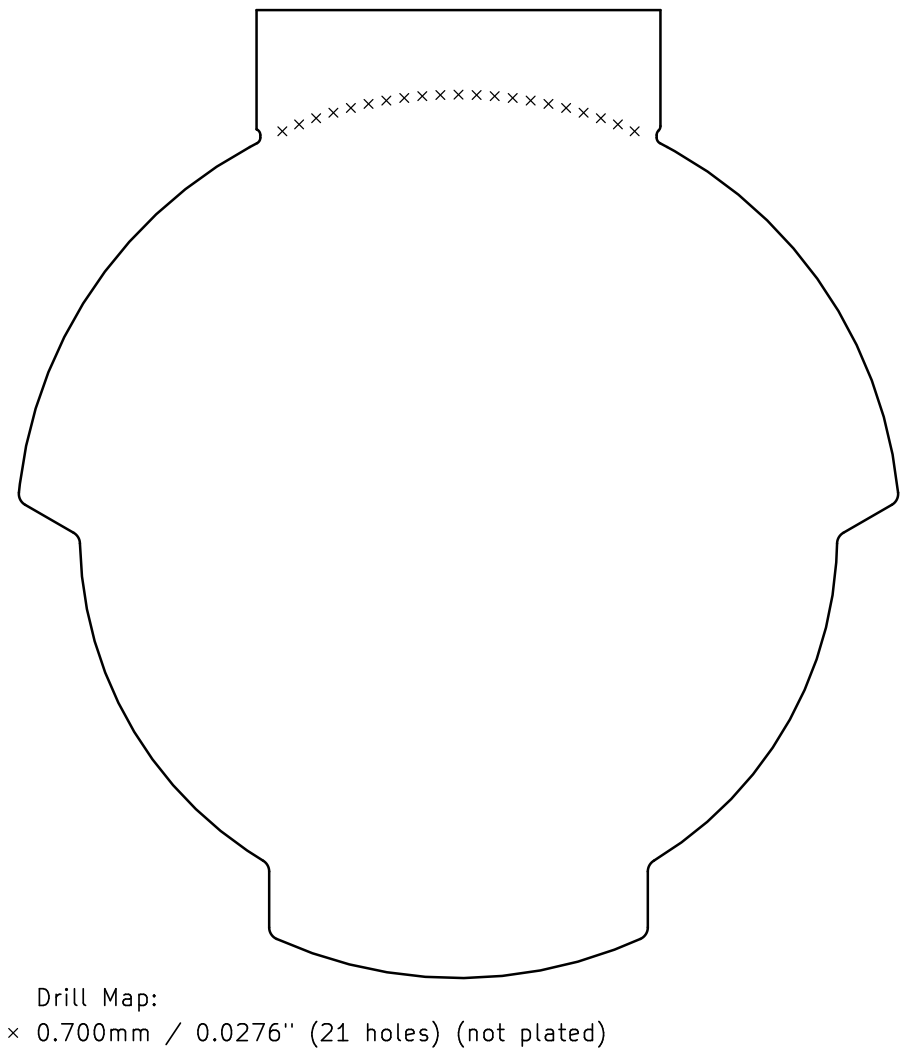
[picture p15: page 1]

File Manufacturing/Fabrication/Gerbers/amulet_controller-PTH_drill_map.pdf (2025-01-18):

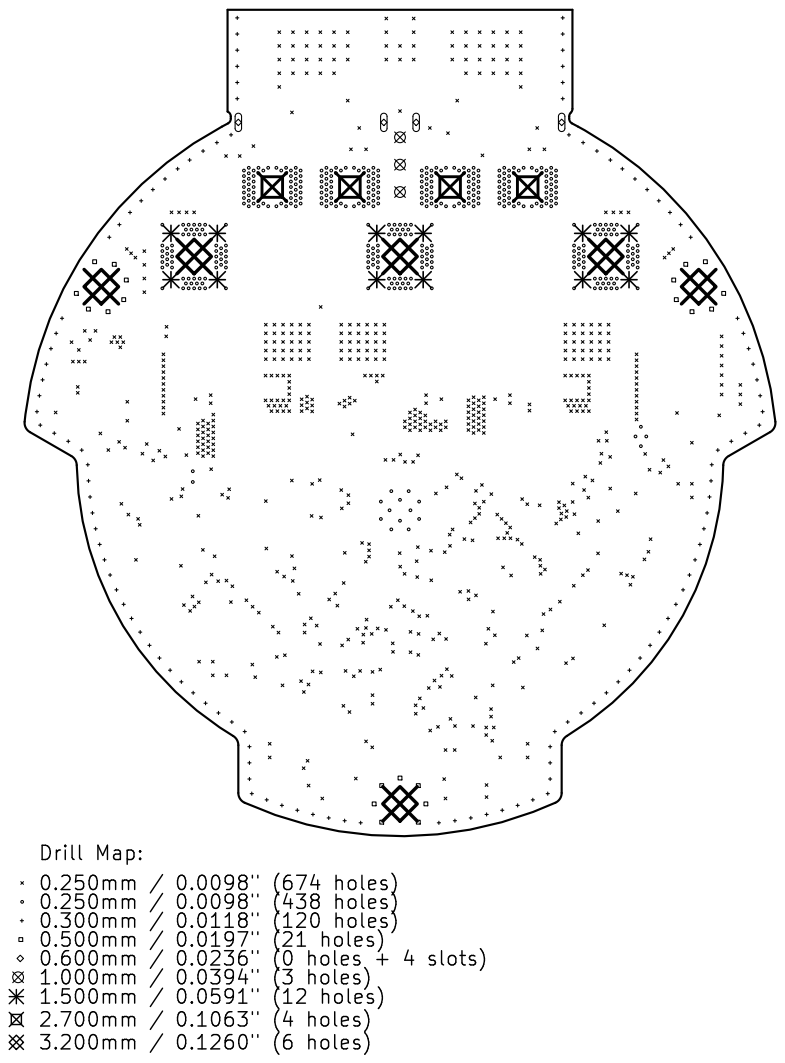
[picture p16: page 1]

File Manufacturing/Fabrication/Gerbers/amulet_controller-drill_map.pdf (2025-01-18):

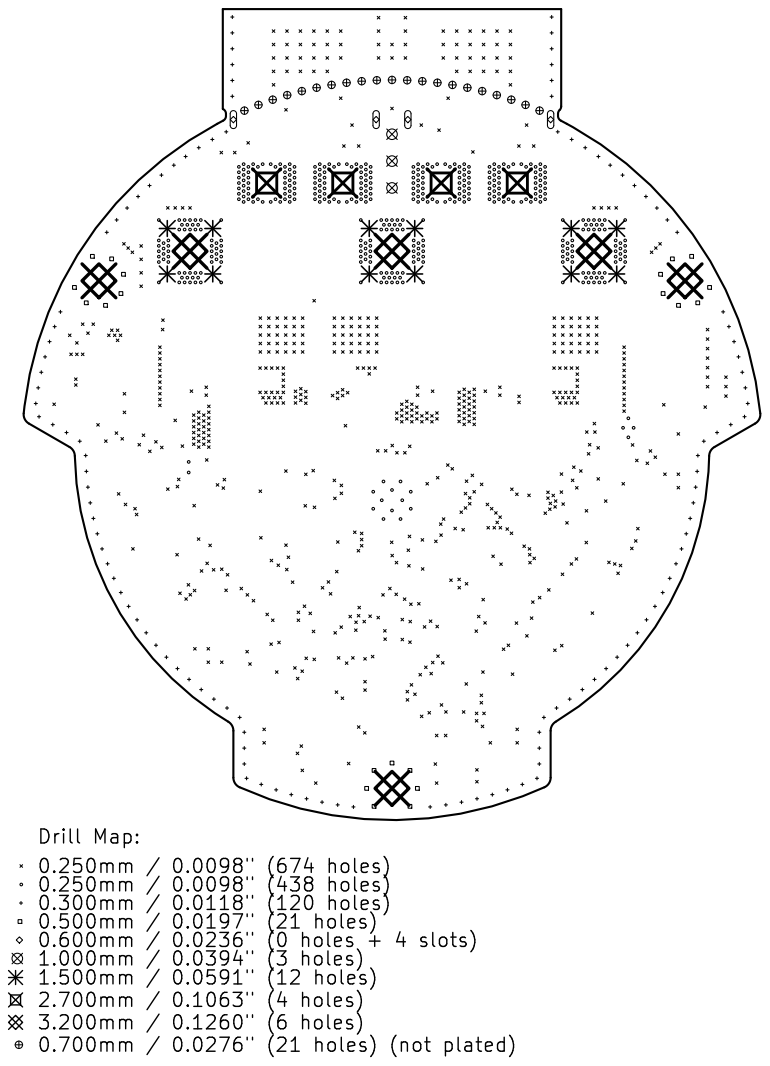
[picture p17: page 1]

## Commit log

2024-11-23 cicd test
    [Block Diagram.kicad_sch, Gate_Resistor_Calculator_V1.xlsx, Interface - FD-CAN.kicad_sch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]
2024-11-23 Update Outputs
    [MCU - Power.kicad_sch, User - LED Indicators.kicad_sch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]
2024-11-24 Update Testpoints
    [amulet_controller-B_Mask_(NO_SNUBBER).gbr, amulet_controller-B_Paste_(NO_SNUBBER).gbr, amulet_controller-B_Silkscreen_(NO_SNUBBER).gbr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]
2024-11-24 remove variant outputs for now
    [Block Diagram.kicad_sch, Interface - FD-CAN.kicad_sch, Interface - Fan Control.kicad_sch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]
2024-11-24 Update PDF Fabrication Document
    [amulet_controller-NPTH.drl, amulet_controller-PTH.drl]
2024-11-24 deleted split
    [Block Diagram.kicad_sch, Interface - FD-CAN.kicad_sch, Interface - Fan Control.kicad_sch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]
2024-11-24 Save changes before switching branches
2024-11-25 uncomment xlsx bom
2024-11-29 add exclude filter
2024-12-01 small changes
    [Block Diagram.kicad_sch, Interface - FD-CAN.kicad_sch, Interface - Fan Control.kicad_sch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]
2024-12-16 automatic ToC
    [Block Diagram.kicad_sch, Interface - FD-CAN.kicad_sch, Interface - Fan Control.kicad_sch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]
2024-12-17 automatic revision history
    [Revision History.kicad_sch]
2024-12-17 Fix alignment
    [Revision History.kicad_sch]
2025-01-18 Updated files without navigate_results
    [Interface - FD-CAN.kicad_sch, Interface - Fan Control.kicad_sch, Interface - Interconnects.kicad_sch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]
2025-01-18 Do not modify pcb on auto-commit
2025-01-18 Small changes to workflow and add drill map to fab
2025-01-18 Fixed kicad_pro file
